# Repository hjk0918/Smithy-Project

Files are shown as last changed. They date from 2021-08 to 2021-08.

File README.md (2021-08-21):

# Physical Prototyping: Smithy
Click here to see demo video:

   IMAGE ALT TEXT (http://www.youtube.com/watch?v=cRNW_WYLdRA "Video Title")

## Project Overview
<p align="center" width="75%">
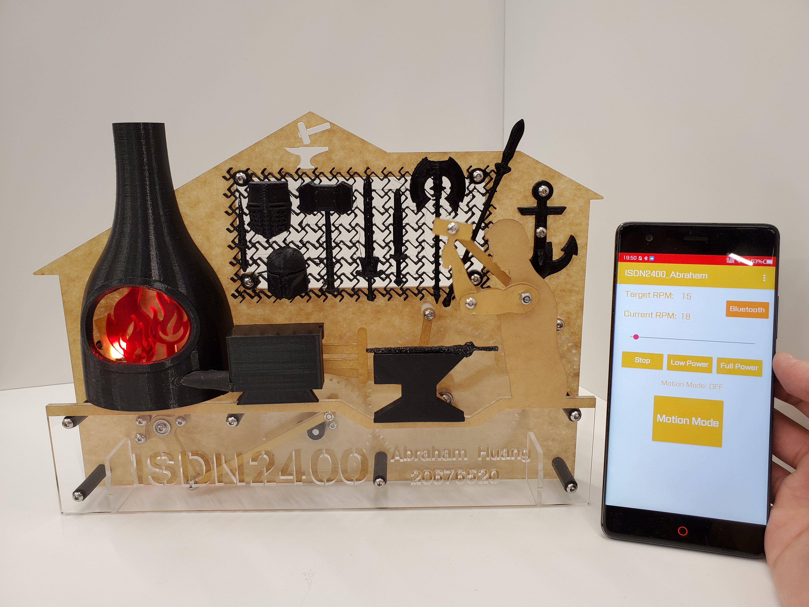
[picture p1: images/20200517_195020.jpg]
  
</p>
 This is my year 1 physical prototyping project for course ISDN2400. This project involves CAD design, 3D printing & scanning, linkage, Arduino, and mobile App. Basically, I created a scene of a traditional smithy. When the system is turned on, the blacksmith starts to strike the unfinished sword with a hammer. The air blower pumps air into the forge while the fire inside the forge is flickering (lighted up by LED) and jumping up and down. The driven motor can be tele-controlled by an Android App with either touching and motion detection.

## Mechanism
<p align="center">
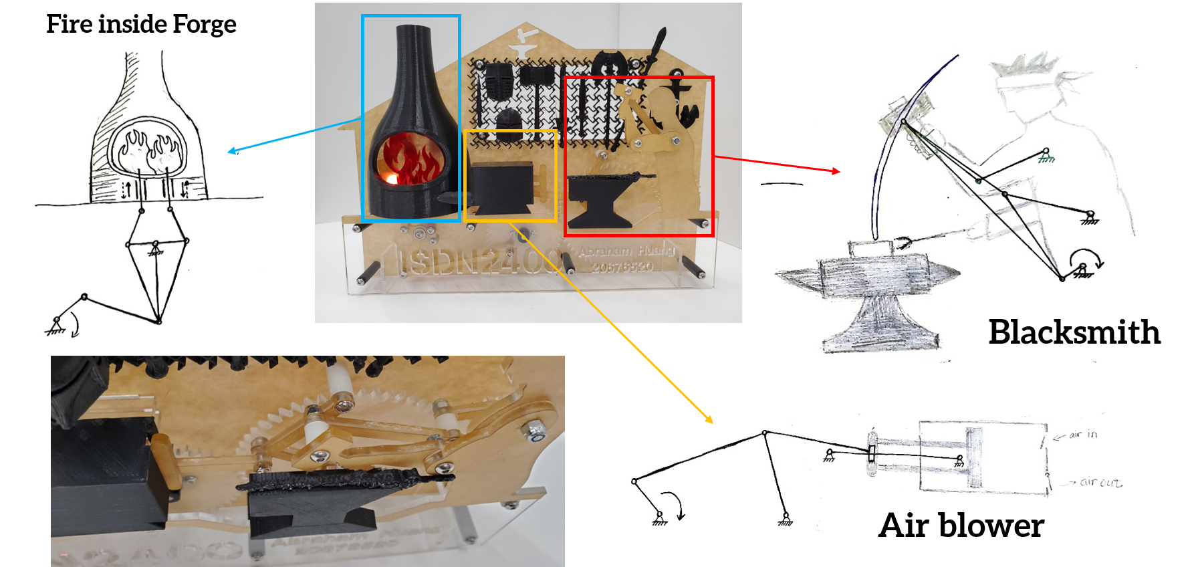
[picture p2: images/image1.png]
  
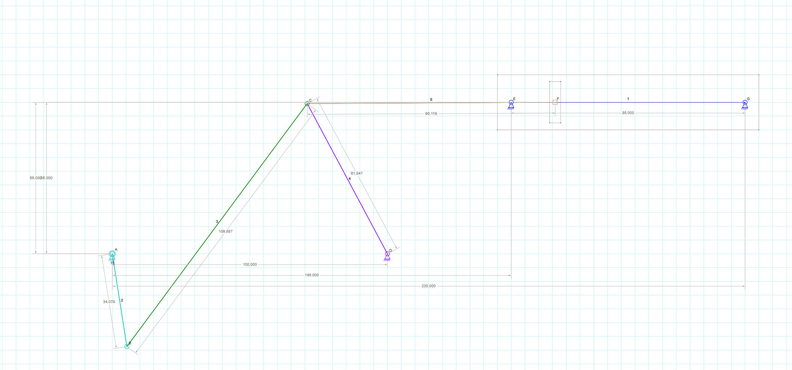
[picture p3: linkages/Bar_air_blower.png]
  
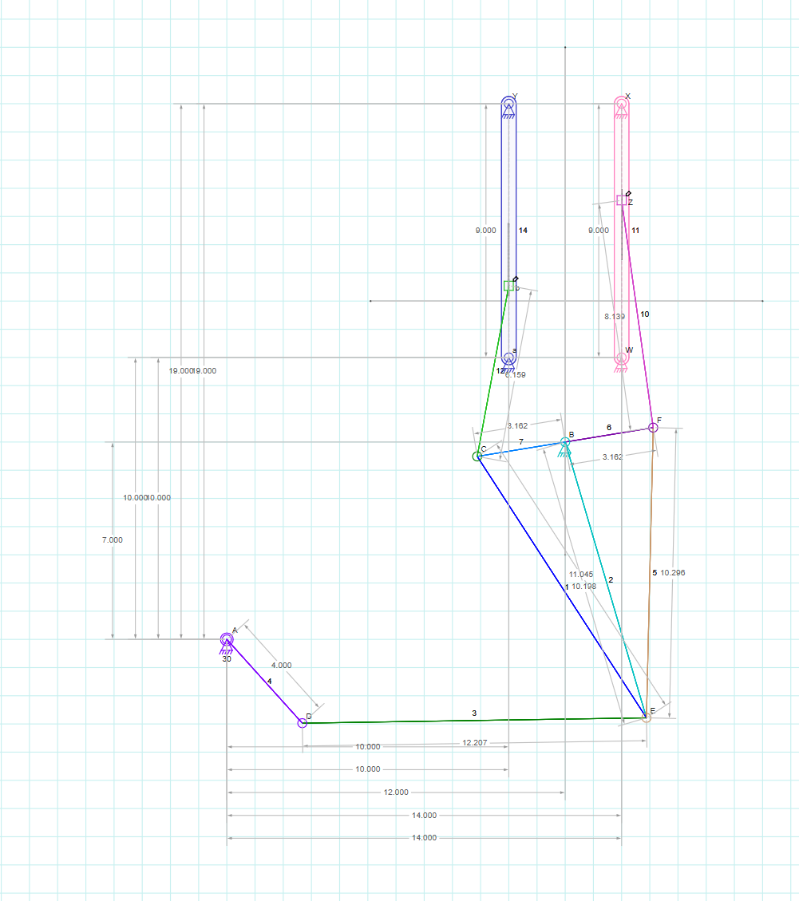
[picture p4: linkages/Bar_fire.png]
  
</p>
The mechanical motion system consists of three parts, the blacksmith, the air blower and the forge. Each part is an extension from four-bar linkage, designed by me. I separately designed each single mechanism, and then combined them all together with gears, so that it can be driven by one motor.

## PID Control
The torque of the linkage system fluctuates while working. At the beginning, I used PWM control to input a constant votage to the motor, but it can’t rotate at a constant speed. So I used PID control regarding to the error between the current RPM and my target RPM. Then the whole system could keep working at a certain speed that I want. 
<p align="center">
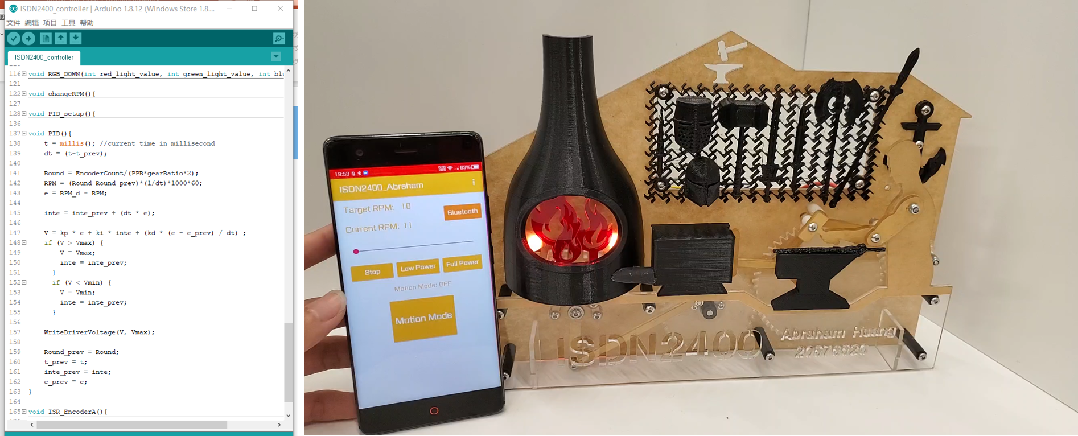
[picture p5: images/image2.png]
  
</p>

## 3D Printing & 3D Scanning
<p align="center">
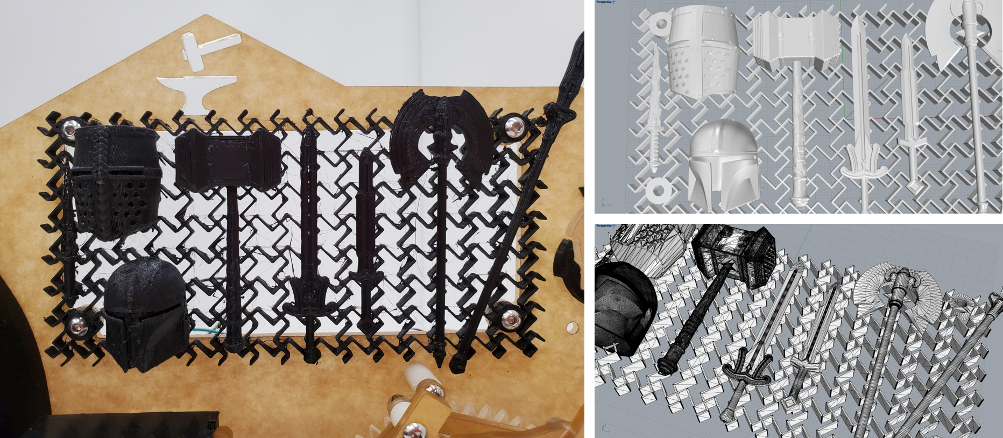
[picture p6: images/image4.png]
  
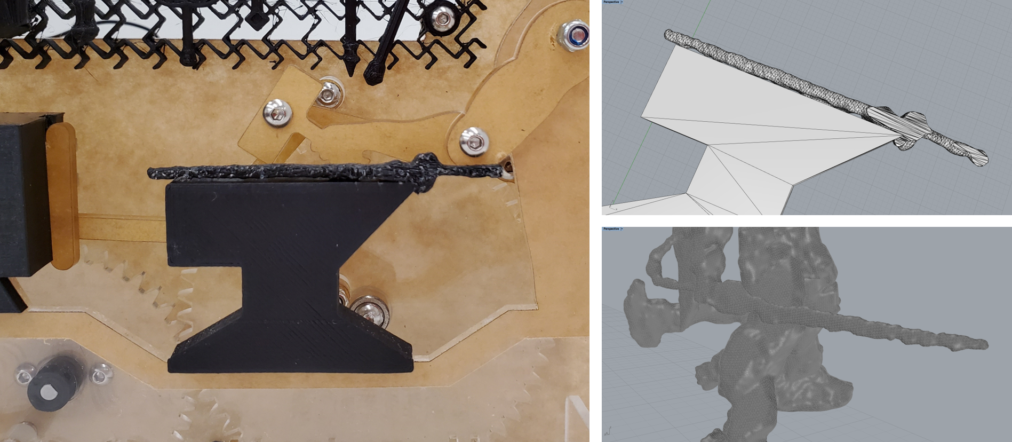
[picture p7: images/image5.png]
  
</p>

## Conclusion
In this project, I spent most of my time on linkage design and PID controller. For mechanical design, It takes me quite a lot of time to adjust dimensions for different linkage systems to fit into one. There were always some unexpected interferences that I should deal with. If I were doing this project once again, I would consider the system as a whole thing at the very beginning. This is also my first time to write a PID controller by myself. Its performance turned out to be so amazing and I'm proud of it.

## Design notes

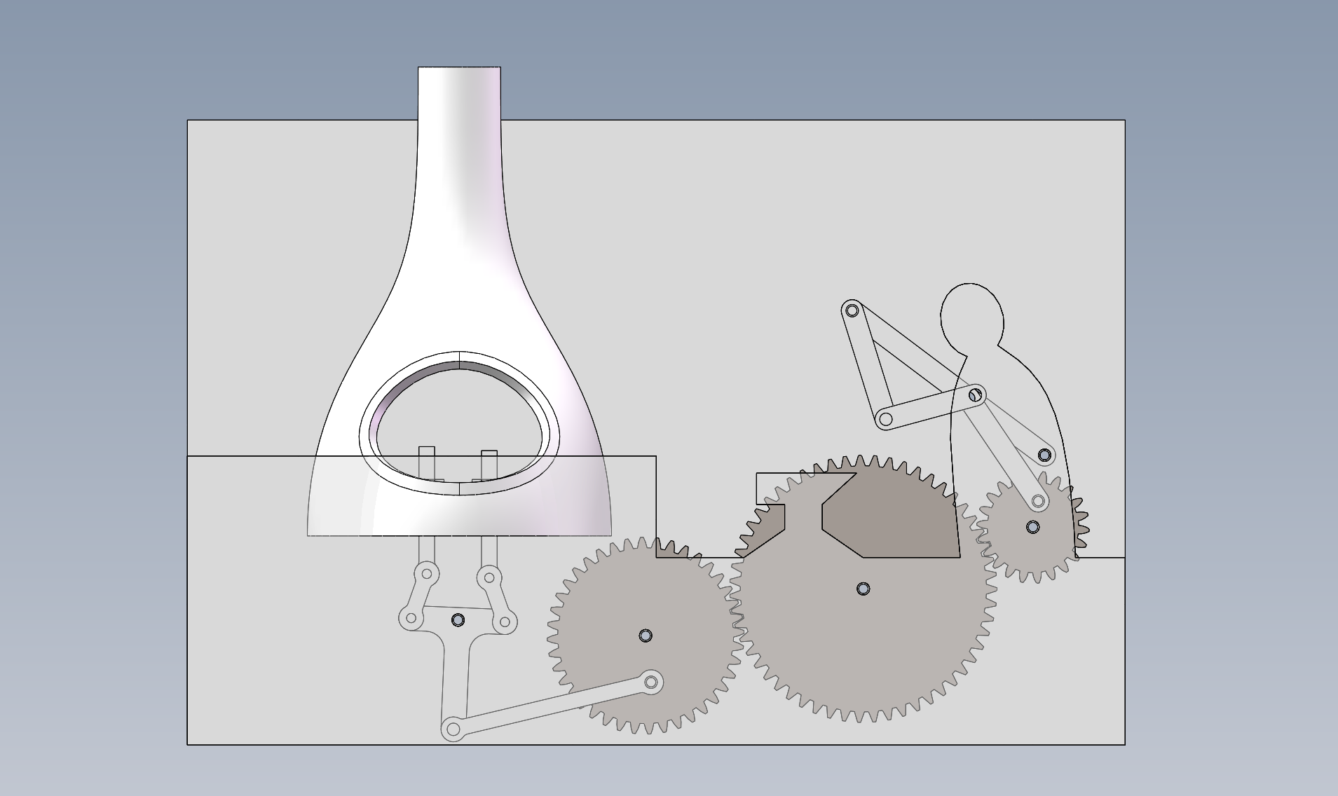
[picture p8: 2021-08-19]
images/roaster_development1.png

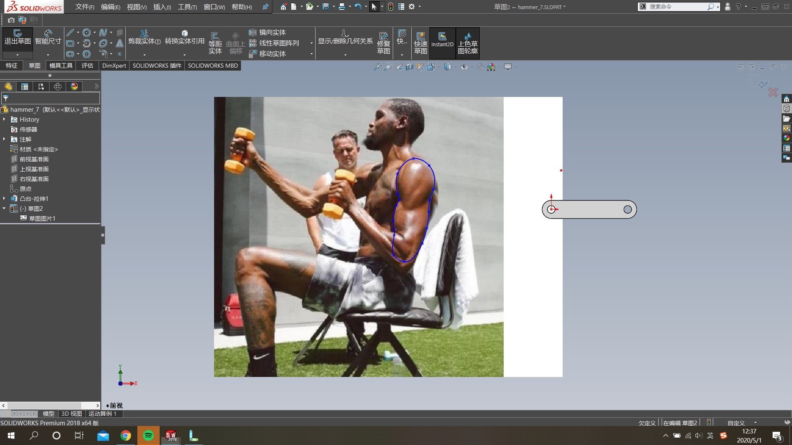
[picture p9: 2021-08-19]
images/upper arm.jpg

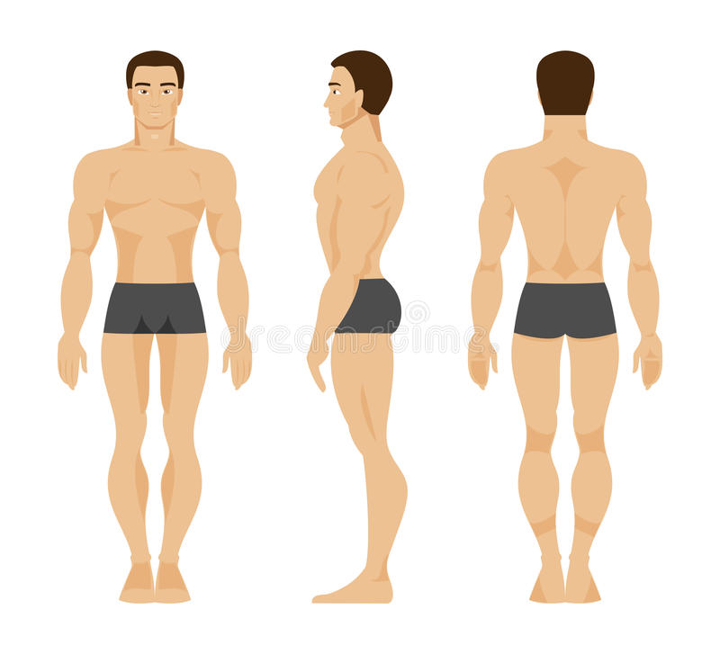
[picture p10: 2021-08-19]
images/human body.jpg

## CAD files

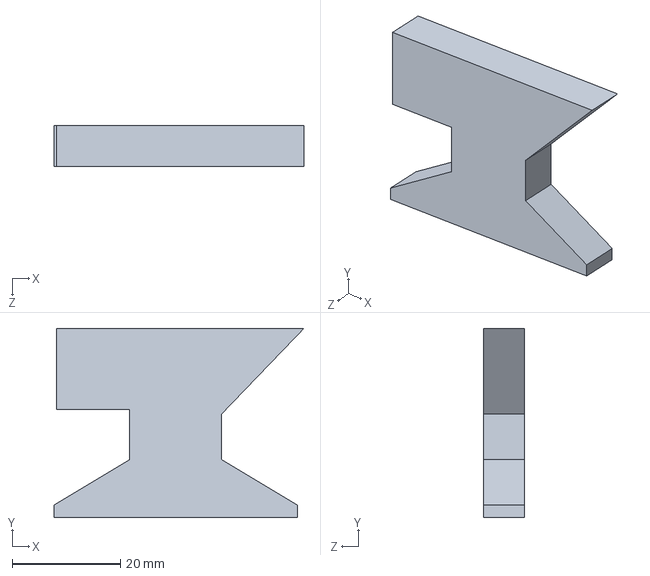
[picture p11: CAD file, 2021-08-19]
CAD Model/anvil^hammer_ASM.sldprt
46.2 x 35.0 x 7.50 mm

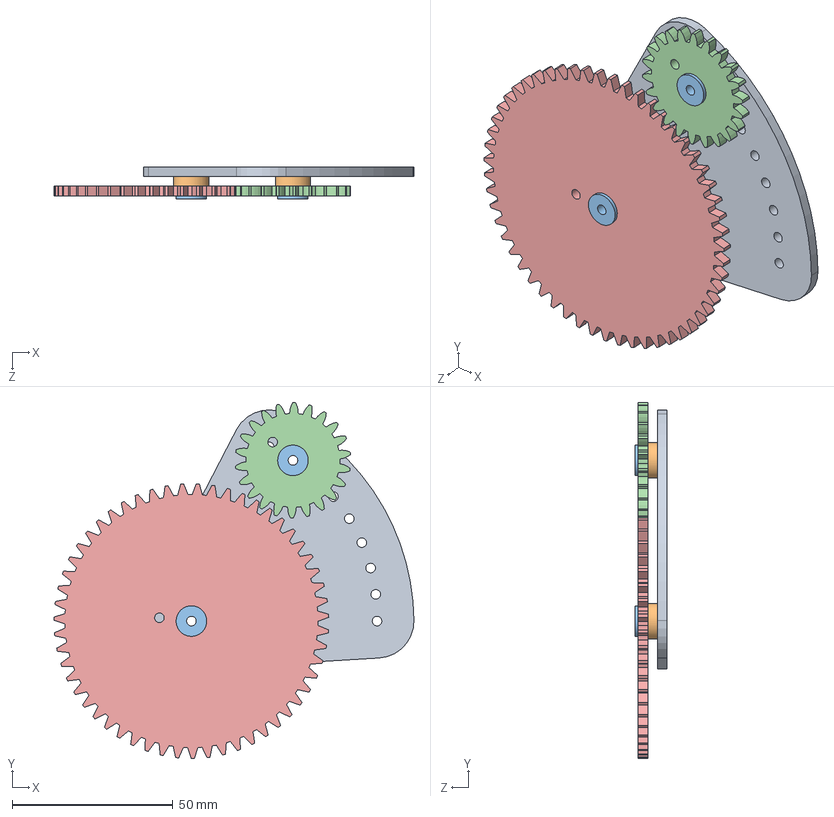
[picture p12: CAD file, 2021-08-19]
CAD Model/GearTest.SLDASM
112.0 x 110.8 x 10.0 mm
test_board
spacer_under_bearing x 2
F693zz_3_8_9.5 x 2
GB - Spur gear 1.5M 22T
GB - Spur gear 1.5M 55T

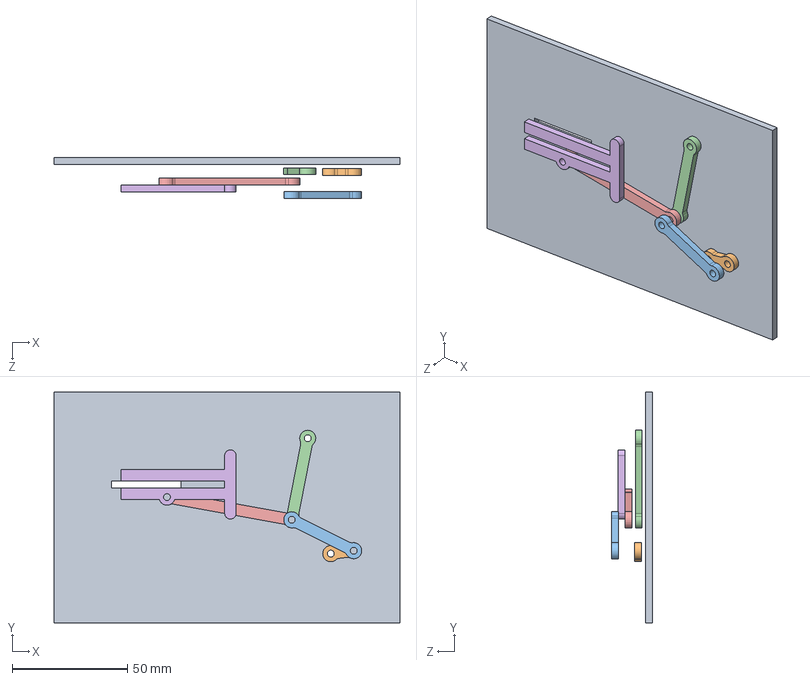
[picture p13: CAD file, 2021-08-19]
CAD Model/air blower/air_blower_ASM.SLDASM
150.0 x 100.0 x 17.6 mm
air_blower_ground
air_blower_2
air_blower_3
air_blower_4
air_blower_5
air_blower_slider

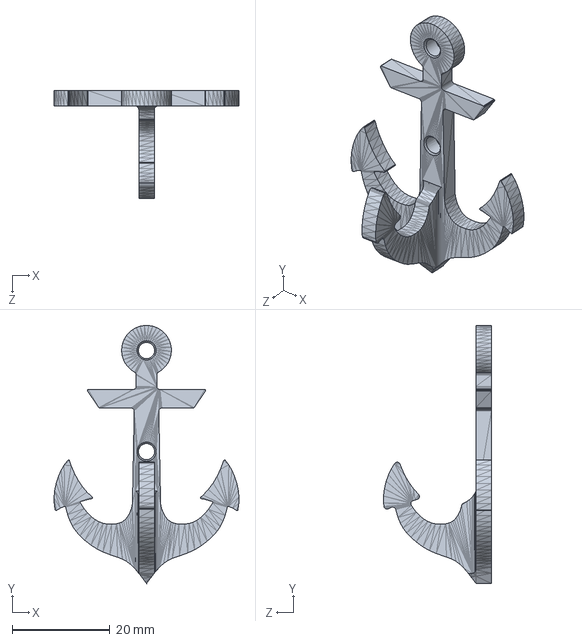
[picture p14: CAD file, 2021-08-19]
CAD Model/3D print/锚钩1.SLDPRT
37.9 x 52.8 x 22.1 mm

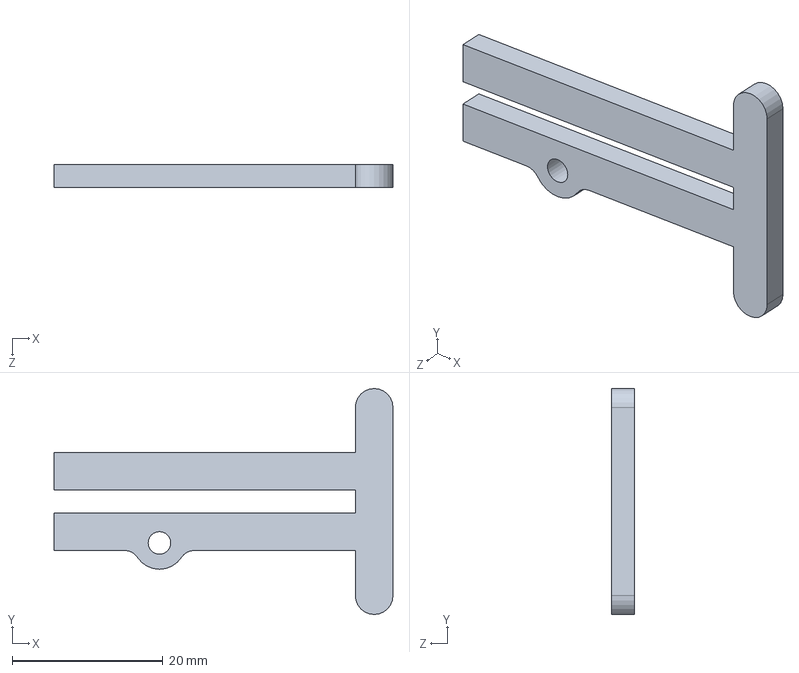
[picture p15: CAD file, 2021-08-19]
CAD Model/air blower/AC3_air_blower_slider.SLDPRT
45.0 x 30.0 x 3.00 mm

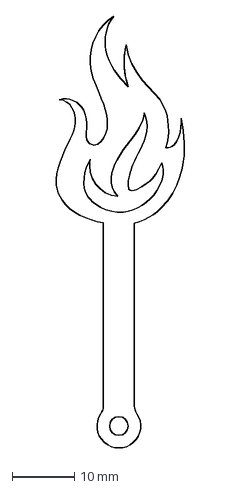
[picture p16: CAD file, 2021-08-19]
CAD Model/DXF/2.5mm Red/AC2R_fire_11_14.DXF
21.1 x 69.5 mm

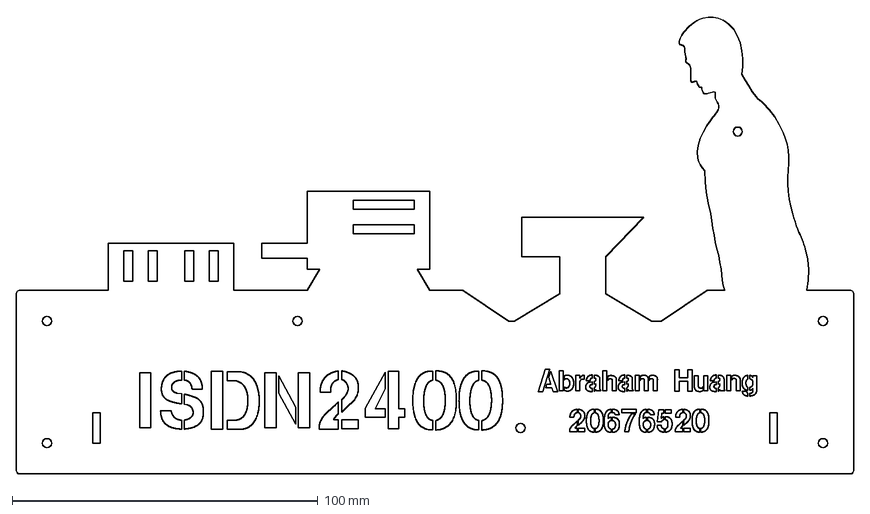
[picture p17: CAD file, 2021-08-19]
CAD Model/DXF/2.5mm White/AC2W_hammer_front.DXF
274.0 x 149.7 mm

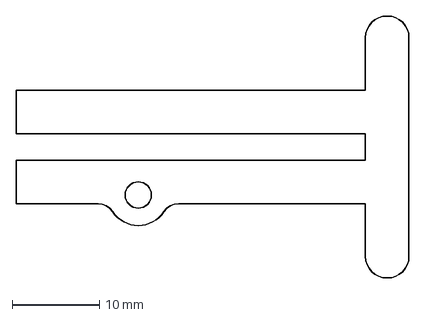
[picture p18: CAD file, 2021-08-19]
CAD Model/DXF/3mm/AC3_air_blower_slider.DXF
45.0 x 30.0 mm

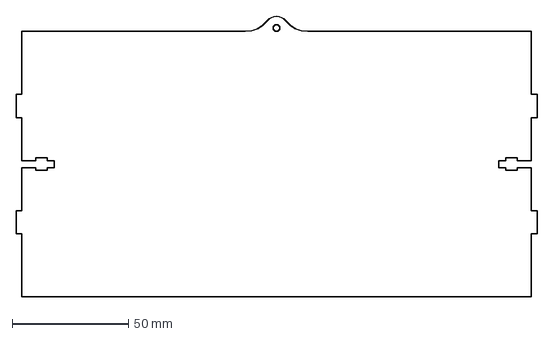
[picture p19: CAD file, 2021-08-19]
CAD Model/DXF/box_down_3.DXF
224.0 x 120.5 mm

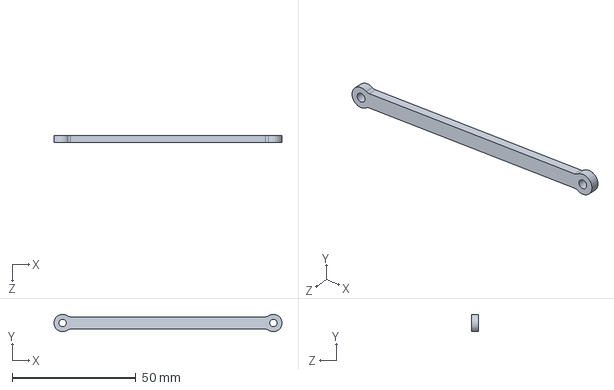
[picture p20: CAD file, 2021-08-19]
CAD Model/hammer/AC3_fire_3.SLDPRT
91.9 x 6.97 x 3.00 mm

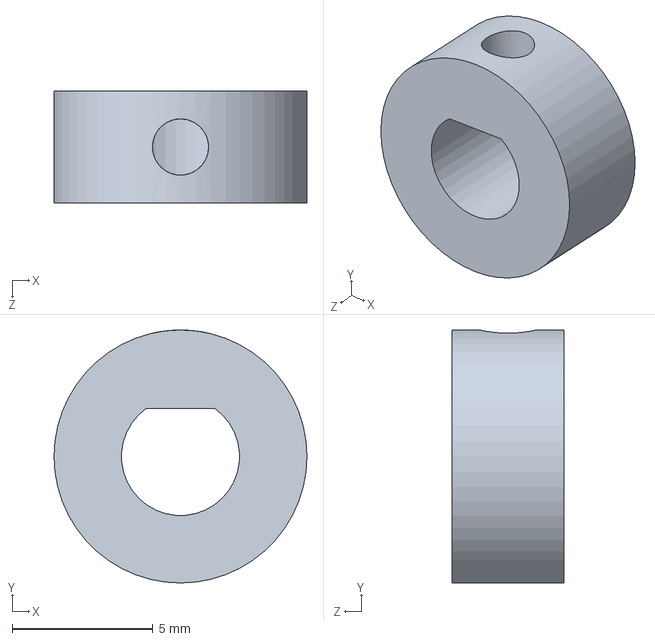
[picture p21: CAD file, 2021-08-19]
CAD Model/3D print/ring.SLDPRT
9.00 x 9.00 x 4.00 mm

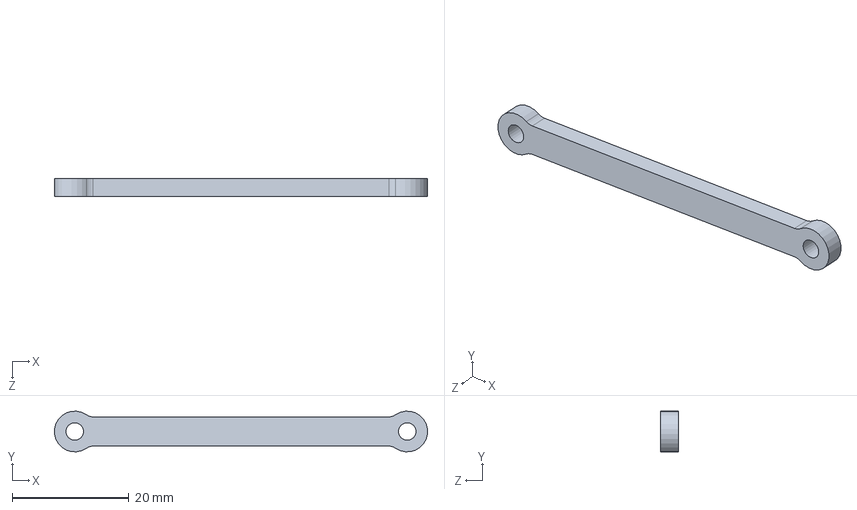
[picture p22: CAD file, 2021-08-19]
CAD Model/air blower/AC3_air_blower_5.SLDPRT
63.9 x 6.97 x 3.00 mm

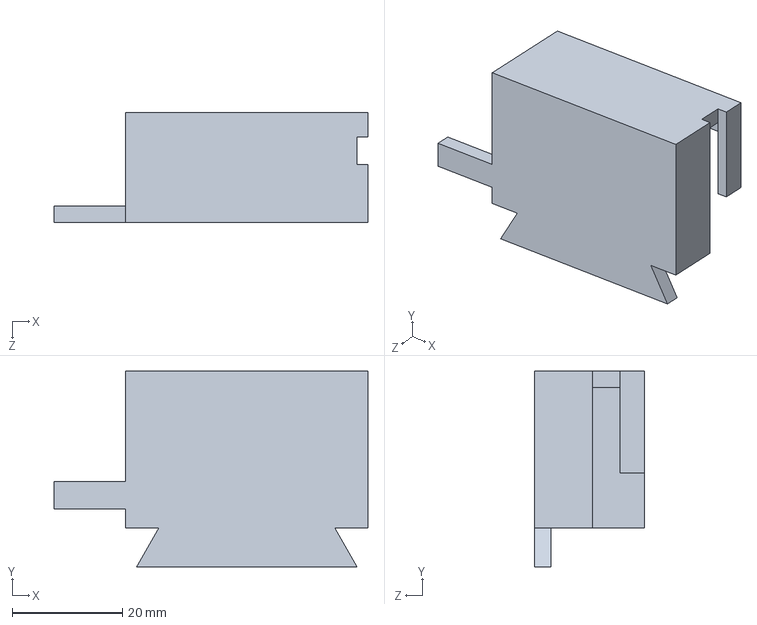
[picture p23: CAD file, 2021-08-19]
CAD Model/air_blower.sldprt
57.0 x 35.5 x 20.0 mm

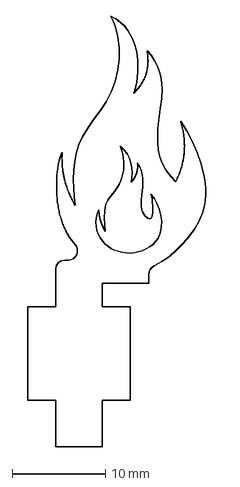
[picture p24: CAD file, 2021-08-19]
CAD Model/DXF/2.5mm Red/AC2R_fire_(3).DXF
19.8 x 46.1 mm

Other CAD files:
CAD Model/DXF/2.5mm White/AC2W_foot.DXF
CAD Model/DXF/3mm/AC3_hammer_7.DXF
CAD Model/DXF/box_side_3.DXF
CAD Model/hammer/AC2R_fire_11_14.SLDPRT
CAD Model/Armor_Board_Auxetic.SLDPRT
CAD Model/DXF/2.5mm Red/AC2R_fire_2.DXF
CAD Model/DXF/2.5mm White/AC2W_hammer_ground.DXF
CAD Model/DXF/3mm/AC3_AC3_air_blower_support_horizontal.DXF
CAD Model/DXF/3mm/AC3_air_blower_3.DXF
CAD Model/DXF/3mm/AC3_air_blower_4.DXF
CAD Model/DXF/3mm/AC3_air_blower_5.DXF
CAD Model/DXF/3mm/AC3_air_blower_support_verticle.DXF
CAD Model/DXF/3mm/AC3_fire_10_12.DXF
CAD Model/DXF/3mm/AC3_fire_12567.DXF
CAD Model/DXF/3mm/AC3_fire_3.DXF
CAD Model/DXF/3mm/AC3_fire_support_small.DXF
CAD Model/DXF/3mm/AC3_fire_support_vertical.DXF
CAD Model/DXF/3mm/AC3_hammer_125.DXF
CAD Model/DXF/3mm/AC3_hammer_4.DXF
CAD Model/DXF/3mm/AC3_hammer_6.DXF
CAD Model/DXF/3mm/AC3_spacer_under_bearing.DXF
CAD Model/DXF/3mm/AC3_spacer_under_motor.DXF
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

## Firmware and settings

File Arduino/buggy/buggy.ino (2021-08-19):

//#include<Servo.h>   // 声明调用Servo.h库
//Servo myservo;      // 创建一个舵机对象
char lr, maohao, n;
int pwm;
int openPos = 110;  //开门位置
int closePos = 40;  //关门位置
  //PWM capable Pin : 3,5,6,9,10,11   but: 9pin,10pin的pwm与servo库冲突
  // LeftMotor
int dir1PinA = 8; 
int dir2PinA  = 7;
int speedPinA = 6;
  // RightMotor
int dir1PinB = 2;
int dir2PinB = 4;
int speedPinB = 5;
  //shovel __ ignore it now
int dir1PinC = 12;
int dir2PinC = 10;
int speedPinC = 11;
  //Servo
int servoPin = 3;

void setup() {
  
  pinMode(dir1PinA, OUTPUT);
  pinMode(dir2PinA, OUTPUT);
  pinMode(speedPinA, OUTPUT);
  pinMode(dir1PinB, OUTPUT);
  pinMode(dir2PinB, OUTPUT);
  pinMode(speedPinB, OUTPUT);
  pinMode(dir1PinC, OUTPUT);
  pinMode(dir2PinC, OUTPUT);
  pinMode(speedPinC, OUTPUT);

  //myservo.attach(servoPin); // 将舵机与声明的舵机对象连接起来
  pinMode(servoPin, OUTPUT);// 设定舵机接口为输出接口

  Serial.begin (9600); //initialise serial port
  
}


void servopulse(int servopin,int myangle)//定义一个脉冲函数
  {
  int pulsewidth=(myangle*11)+500;//将角度转化为500-2480 的脉宽值
  for(int i=0;i<=40;i++){
    digitalWrite(servoPin,HIGH);//将舵机接口电平至高
    delayMicroseconds(pulsewidth);//延时脉宽值的微秒数
    digitalWrite(servoPin,LOW);//将舵机接口电平至低
    delay(20-pulsewidth/1000);
  }
}

void loop() {
  // put your main code here, to run repeatedly:
  if (Serial.available () > 0){ //when serial buffer receive data
    String s;
    boolean p;

    //读左右
    lr = Serial.read();
    delay(10);//Serial.println(lr);

    //读冒号
    maohao = Serial.read();
    delay(10);//Serial.println(l);

    //读数字
    n = Serial.read();
    while(n != '&'){
      //Serial.println(n);
      s += (char)n;
      n = Serial.read();
    }
    Serial.println(s);
    pwm = s.toInt(); //得到pwm数值
    delay(20);

    if (lr == '1'){           //left motor
      if(pwm > 0){
        digitalWrite(dir1PinA, HIGH);
        digitalWrite(dir2PinA, LOW);
      }else{
        digitalWrite(dir1PinA, LOW);
        digitalWrite(dir2PinA, HIGH);
      }
      analogWrite(speedPinA, abs(pwm));
    }else if(lr == '2'){      //right motor
      if(pwm > 0){        
        digitalWrite(dir1PinB, HIGH);
        digitalWrite(dir2PinB, LOW);
      }else{
        digitalWrite(dir1PinB, LOW);
        digitalWrite(dir2PinB, HIGH);
      }
      analogWrite(speedPinB, abs(pwm));
    }else if(lr == '3'){      //shovel motor __ ignore it now
      if(pwm > 0){
        digitalWrite(dir1PinC, HIGH);
        digitalWrite(dir2PinC, LOW);
      }else{
        digitalWrite(dir1PinC, LOW);
        digitalWrite(dir2PinC, HIGH);
      }
      analogWrite(speedPinC, abs(pwm));
    }else if(lr == '4'){      //shovel motor step by step
      if(pwm > 0){
        digitalWrite(dir1PinC, HIGH);
        digitalWrite(dir2PinC, LOW);
      }else{
        digitalWrite(dir1PinC, LOW);
        digitalWrite(dir2PinC, HIGH);
      }
      analogWrite(speedPinC, 255);
      delay(30);
      analogWrite(speedPinC, 0);
    }
    else if(lr == '5'){     //both wheels
      if(pwm > 0){        
        digitalWrite(dir1PinA, HIGH);
        digitalWrite(dir2PinA, LOW);
        digitalWrite(dir1PinB, HIGH);
        digitalWrite(dir2PinB, LOW);
      }else{
        digitalWrite(dir1PinA, LOW);
        digitalWrite(dir2PinA, HIGH);
        digitalWrite(dir1PinB, LOW);
        digitalWrite(dir2PinB, HIGH);
      }
      analogWrite(speedPinA, abs(pwm));
      analogWrite(speedPinB, abs(pwm));
      
    }else if(lr == '6'){    //Servo Open
        servopulse(servoPin,openPos);//引用脉冲函数
    }else if(lr == '7'){    //Servo Close
        servopulse(servoPin,closePos);//引用脉冲函数
    }
  }
}


/*void setServo(int pos){
  int curPos = myservo.read(); //读取当前舵机位置
  if(curPos >= pos){
    for(int i = curPos; i > pos; i--){
      myservo.write(pos);
      delay(5);
    }
  }else{
    for(int i = curPos; i < pos; i++){
      myservo.write(i);
      delay(5);
    }
  }
}*/

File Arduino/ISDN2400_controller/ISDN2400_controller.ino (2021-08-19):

#include <SoftwareSerial.h>
SoftwareSerial BT(12, 13);
//PID
float kp = 0.18;
float ki = 0.003;
float kd = 0.045;
float e, e_prev = 0, inte, inte_prev=0;

float t, t_prev, dt;
float Round, Round_prev = 0, RPM=0, RPM_d=5, RPM_h;

//Encoder
const byte interruptPinA = 2;
const byte interruptPinB = 4;
long EncoderCount = 0;

//Motor
int PWMPin = 5;
int DirPin1 = 7; 
int DirPin2 = 8;
const float PPR = 11; //pulse per revolution
const int gearRatio = 45;
float Vmax = 12;
float Vmin = -12;
float V = 0.1;

//RGB
int RGB_UP_R = 11;
int RGB_UP_G = 10;
int RGB_DOWN_R = 9;
int RGB_DOWN_G = 6;
int RGB_count = 255;
int RGB_freq = 10;
bool RGB_countdown = true;

volatile unsigned long count = 0;
unsigned long count_prev = 0;

void setup() {
  pinMode(interruptPinA, INPUT_PULLUP);
  pinMode(interruptPinB, INPUT_PULLUP);
  attachInterrupt(digitalPinToInterrupt(interruptPinA), ISR_EncoderA, CHANGE);
  attachInterrupt(digitalPinToInterrupt(interruptPinB), ISR_EncoderB, CHANGE);
  Serial.begin(115200);
  //Serial.println("BT is ready!");
  BT.begin(9600);

  pinMode(DirPin1, OUTPUT);
  pinMode(DirPin2, OUTPUT);
  pinMode(PWMPin, OUTPUT);
  pinMode(RGB_UP_R, OUTPUT);
  pinMode(RGB_UP_G, OUTPUT);
  pinMode(RGB_DOWN_R, OUTPUT);
  pinMode(RGB_DOWN_G, OUTPUT);
  
  count = 0;
  PID_setup();
  RGB_setup();
}

void loop() {
  // put your main code here, to run repeatedly:
  if (BT.available () > 0){
    changeRPM();
    PID_setup();
  }
  RGB_update();
  PID();
  if(count%20==0){
    BT.print(String(RPM));
  }
  
  delay(10);
  count++;
  //Serial.print(RPM_d); Serial.print('\t');
  Serial.print(128); Serial.print('\t');
  Serial.println(RPM_h);
  
  
  
}

void RGB_setup(){
  int RGB_count = 255;
  bool RGB_countdown = true;
}

void RGB_update(){
  if(RPM!=0){
    RGB_freq = RPM/10+2;
  }else{
    RGB_freq = 3;
  }
  RGB_DOWN((255+3*RGB_count)/4,RGB_count/5,0);
  RGB_UP(RGB_count,0,0);

  if(RGB_countdown == false){
    RGB_count += RGB_freq;
  }else{
    RGB_count -= RGB_freq;
  }
  if(RGB_count <= 0){
    RGB_count = 0;
    RGB_countdown = false;
  }else if(RGB_count >= 255){
    RGB_count = 255;
    RGB_countdown = true;
  }
}

void RGB_UP(int red_light_value, int green_light_value, int blue_light_value){
  analogWrite(RGB_UP_R, red_light_value);
  analogWrite(RGB_UP_G, green_light_value);
  //analogWrite(RGB_UP_B, blue_light_value);
}

void RGB_DOWN(int red_light_value, int green_light_value, int blue_light_value){
  analogWrite(RGB_DOWN_R, red_light_value);
  analogWrite(RGB_DOWN_G, green_light_value);
  //analogWrite(RGB_DOWN_B, blue_light_value);
}

void changeRPM(){
    String s;
    s=BT.readStringUntil('&');
    RPM_d = s.toInt();   
}

void PID_setup(){
  e=0;
  e_prev = 0;
  inte=0;
  inte_prev=0;
  //WriteDriverVoltage(2,12);
  //delay(50);
}

void PID(){
    t = millis(); //current time in millisecond
    dt = (t-t_prev);
    
    Round = EncoderCount/(PPR*gearRatio*2);
    RPM = (Round-Round_prev)*(1/dt)*1000*60;
    //RPM_h = RPM/22*40;
    e = RPM_d - RPM;
    
    inte = inte_prev + (dt * e);

    V = kp * e + ki * inte + (kd * (e - e_prev) / dt) ;
    if (V > Vmax) {
        V = Vmax;
        inte = inte_prev;
      }
      if (V < Vmin) {
        V = Vmin;
        inte = inte_prev;
      }
  
    WriteDriverVoltage(V, Vmax);
  
    Round_prev = Round;
    t_prev = t;
    inte_prev = inte;
    e_prev = e;
}

void ISR_EncoderA(){
  bool PinB = digitalRead(interruptPinB);
  bool PinA = digitalRead(interruptPinA);

  if(PinB == LOW){
    if(PinA == HIGH){
      EncoderCount++;
    }
    else{
      EncoderCount--;
    }
  }
  else{
    if(PinA == HIGH){
      EncoderCount--;
    }
    else{
      EncoderCount++;
    }
  }
}

void ISR_EncoderB(){
  bool PinB = digitalRead(interruptPinB);
  bool PinA = digitalRead(interruptPinA);

  if(PinA == LOW){
    if(PinB == HIGH){
      EncoderCount--;
    }
    else{
      EncoderCount++;
    }
  }
  else{
    if(PinB == HIGH){
      EncoderCount++;
    }
    else{
      EncoderCount--;
    }
  }
}

void WriteDriverVoltage(float V, float Vmax) {
  int PWMval = int(255 * abs(V) / Vmax);
  if (PWMval > 255) {
    PWMval = 255;
  }
  if (V > 0) {
    digitalWrite(DirPin1, HIGH);
    digitalWrite(DirPin2, LOW);
  }
  else if (V < 0) {
    digitalWrite(DirPin1, LOW);
    digitalWrite(DirPin2, HIGH);
  }
  else {
    digitalWrite(DirPin1, LOW);
    digitalWrite(DirPin2, LOW);
  }
  analogWrite(PWMPin, PWMval);
}
